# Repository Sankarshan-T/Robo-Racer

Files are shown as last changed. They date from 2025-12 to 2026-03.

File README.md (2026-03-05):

# Robo-Racer
Building a RC racing robot capable of navigating sand pits, ramps and a lot more fun stuff.
This project was made because I was always fond of rc cars and I wanted to try something new.

https://github.com/user-attachments/assets/db7c474e-a4ad-4f39-b993-d5889bbc2405

### NO CODE NEEDED FOR THIS ROBOT

## Electronics Required
1. Electrocraze 20D dual channel ESC (1 (Controls the bot without code)
2. Flysky FSi6X Transmitter and receiver (1) (A remote control for the bot)
3. Johnson DC motors 1000 RPM 12V (4) (motors for the bot  to  move)
4. Lipo Battery 3S 2200mAh  (A battery to power the motors)
5. XT-60 connector for battery (A connector for the battery)


## Chassis Design
The chassis design for the model can be found in the CAD folder along with sliced files for 3D printing.


## Assembly Instructions
1. Fit the 4 motors into the chassis.
2. Solder the front left and rear left motor terminals together as one and connect it to the M1A and M1B terminals of the ESC (one for each terminal of the motor)
3. Solder the front right and rear right motor terminals together as one and connect it to the M2A and M2B terminals of the ESC (one for each terminal of the motor)
4. Solder an XT 60 connector to the ESC (+ to + and - to -)
5. Tape up all the joints with insulation tape to prevent shorts
6. Connect channel 2 on receiver to the left output of the ESC and channel 4 to the right.
## Radio Calibration
1. Go to setup->mixes->mix 1, set channel 2 as master and ch4 as slave, -100% for both positive and negative mix.
2. Go to setup->mixes->mix2, set ch4 as master and ch2 as slave, +100% for both.
3. Go to setup->reverse, and set ch4 for reverse on, rest off.

## Images
### 3D Model  
### Wiring diagram 

## BOM, With link to BOM.csv
# https://github.com/Sankarshan-T/Robo-Racer/blob/main/BOM.csv

| Component | Qty |	Price per item | Total Cost | Link |
| --- | --- | --- | --- | ---- |
| Johnson Motors 12V 1000rpm | 4 | 280inr | 1120inr | [Link for Motors](https://ifuturetech.org/product/12v-1000-rpm-johnson-geared-dc-motor-grade-b/) |
| electocraze 20D ESC | 1 | 3200inr | 3200inr | [Link for ESC](https://www.technobotix.in/products/electrocraze-20d-bd-dual-channel-20amp-brushed-motor-controller/1781252000002857099) |
| Wheels | 4 | 150inr | 600inr | [Link for wheels](https://robu.in/product/65mm-robot-smart-car-12-rim-wheel-blue/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) |
| Flysky FSi6X + receiver 6ch | 1 | 4900inr | 4900inr | [Link for transmitter + reciever](https://www.flyrobo.in/flysky-fs-i6x-2.4ghz-6ch-afhds-2a-rc-transmitter-with-fs-ia10b-2.4ghz-10ch-receiver) |
| LiPo battery 3s 2200mah	 | 1 | 1500inr | 1500inr | [Link for battery](https://robu.in/product/orange-2200mah-3s-30c60c-lithium-polymer-battery-pack-lipo/) |
| Chassis 3D printed | 1 | 300inr | 300inr | No Link |
| Solder | 1 | 80inr | 80inr | [Link for Solder](https://www.amazon.in/7Q7-Electronic-Soldering-50Grams-Solder-Wire/dp/B07ZLR38MB) |
| Tape | 1 | 15inr | 15inr | [Link for Tape](https://blinkit.com/prn/steelgrip-pvc-electrical-insulation-tape/prid/425578) |
| ---- | - | Total: | 11715inr | ---- |

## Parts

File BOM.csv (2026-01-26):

Component | Qty | Price per item | Total Cost | Link
Johnson Motors 12V 1000rpm | 4 | 280 | 1120 | https://ifuturetech.org/product/12v-1000-rpm-johnson-geared-dc-motor-grade-b/
electocraze 20D ESC | 1 | 3200 | 3200 | https://www.technobotix.in/products/electrocraze-20d-bd-dual-channel-20amp-brushed-motor-controller/1781252000002857099
Wheels | 4 | 150 | 600 | https://robu.in/product/65mm-robot-smart-car-12-rim-wheel-blue/?gad_source=1&gad_campaignid=20387462343
Flysky FSi6X + receiver 6ch | 1 | 4900 | 4900 | https://www.flyrobo.in/flysky-fs-i6x-2.4ghz-6ch-afhds-2a-rc-transmitter-with-fs-ia10b-2.4ghz-10ch-receiver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
LiPo battery 3s 2200mah | 1 | 1500 | 1500 | https://robu.in/product/orange-2200mah-3s-30c60c-lithium-polymer-battery-pack-lipo/
Chassis 3D printed | 1 | 300 | 300
Solder | 1 | 80 | 80 | https://www.amazon.in/7Q7-Electronic-Soldering-50Grams-Solder-Wire/dp/B07ZLR38MB
Tape | 1 | 15 | 15 | https://blinkit.com/prn/steelgrip-pvc-electrical-insulation-tape/prid/425578
 |  | Total | 11715inr

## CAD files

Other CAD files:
CAD Files/body.step
CAD Files/spoiler.step
CAD Files/body.stl
CAD Files/roboracer_chassis.f3d
CAD Files/roboracer_spoiler.f3d
CAD Files/spoiler.stl

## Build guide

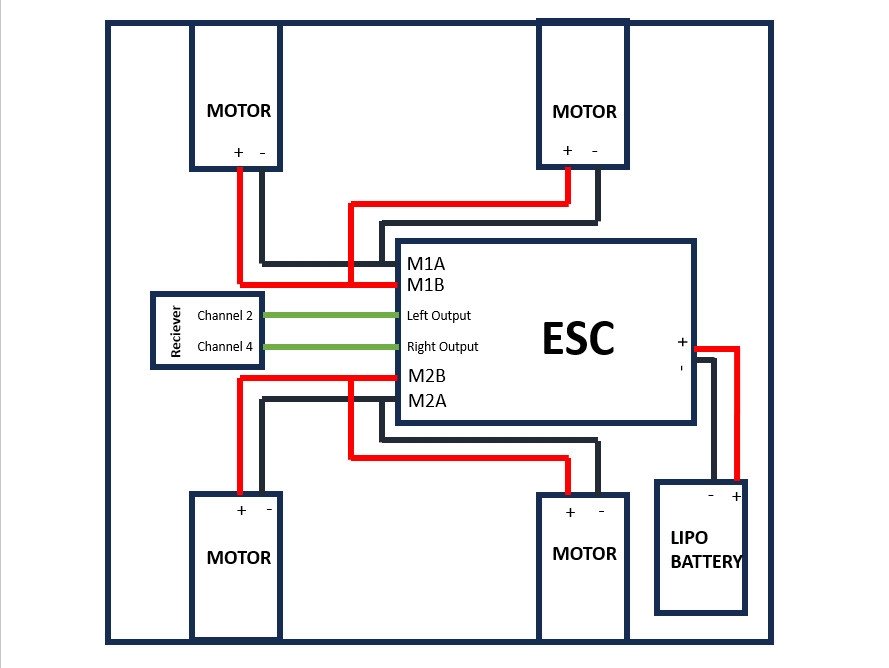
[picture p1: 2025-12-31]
Wiring diagram.png

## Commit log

2025-11-29 Rename to Chassis
2025-11-29 Rename to Chassis Back
2025-11-29 Rename to Sample track for testing model
2025-11-29 Add BOM.csv with bill of materials
    [BOM.csv]
2025-12-15 Enhance README with electronics and assembly details
    Added detailed instructions for electronics, chassis design, assembly, and radio calibration.
2025-12-15 added files
    uploaded files
    [body.stl, spoiler.stl]
2025-12-15 bom updated
    [BOM.csv, BOM.xlsx]
2025-12-16 Fix total currency format in BOM.csv
    [BOM.csv]
2025-12-31 wiring diagram
2026-01-26 added .step files
    [body.step, spoiler.step]
2026-01-26 Update README with images and BOM information
    Added images, BOM details, and links to components.
2026-01-26 Fix links for Solder and Tape in README
2026-01-26 uploaded f3d
    [roboracer_chassis.f3d, roboracer_spoiler.f3d]
